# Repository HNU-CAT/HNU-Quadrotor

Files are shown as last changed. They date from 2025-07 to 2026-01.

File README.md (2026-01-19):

# HNU-Quadrotor

<figure>
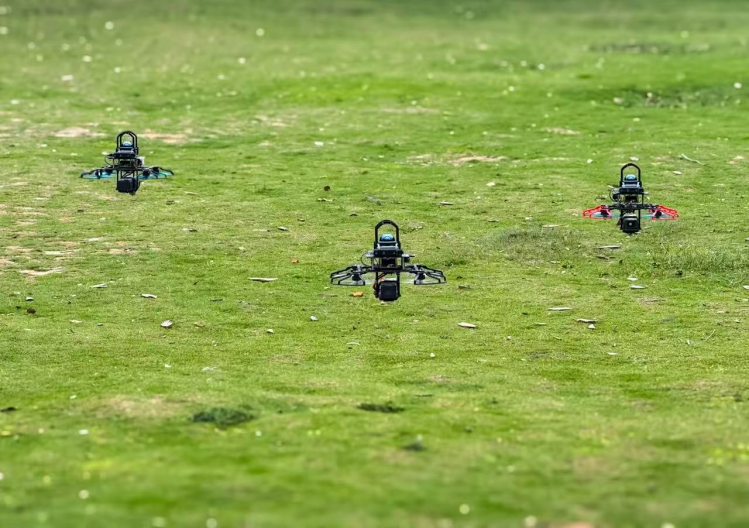
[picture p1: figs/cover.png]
    
    <figcaption>Three drones flying in the wild</figcaption>
</figure>

<figure>
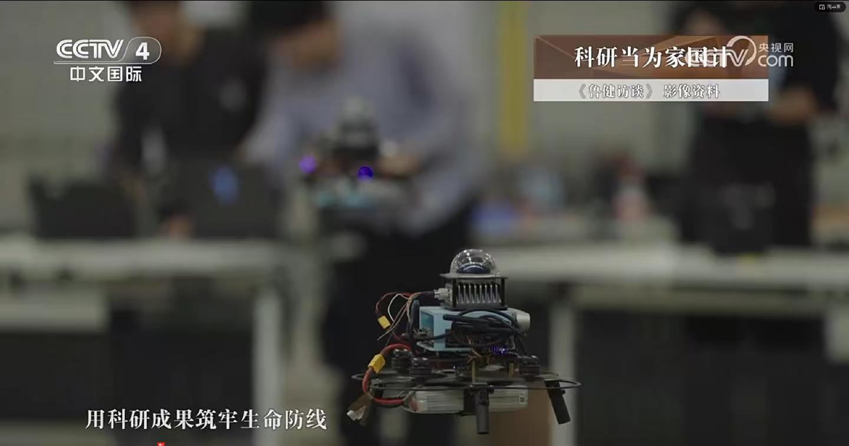
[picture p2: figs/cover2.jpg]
    
    <figcaption>Design of the first generation of drones</figcaption>
</figure>

<figure>
    
    <figcaption>>Four drones flying indoors</figcaption>
</figure>

**Author：**[WHDworld](https://github.com/WHDworld), [XXLiu-HNU](https://github.com/XXLiu-HNU)

## Provided Materials

We provide the following resources:

* Editable drafts and assemblies [./hardware](./hardware)

| Caption | Image Display |
|---|---|
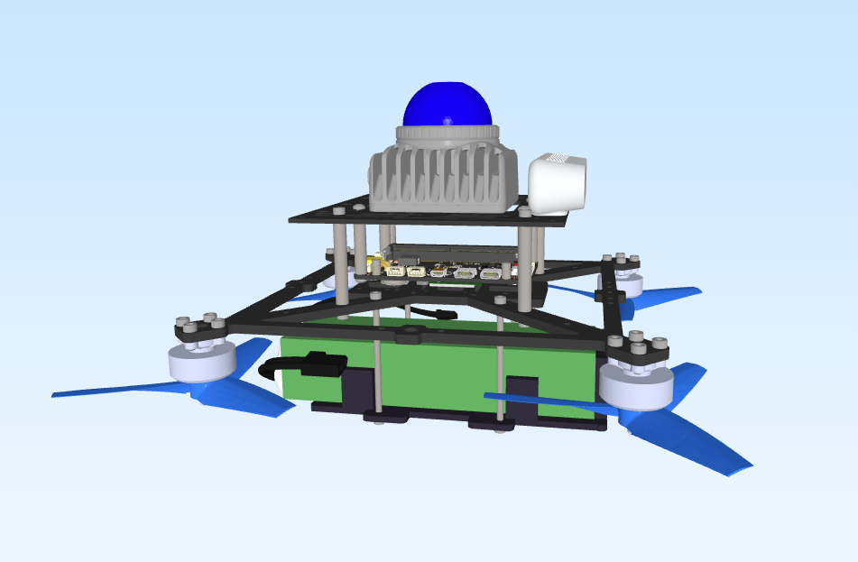
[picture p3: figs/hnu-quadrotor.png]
| UAV complete machine |  |
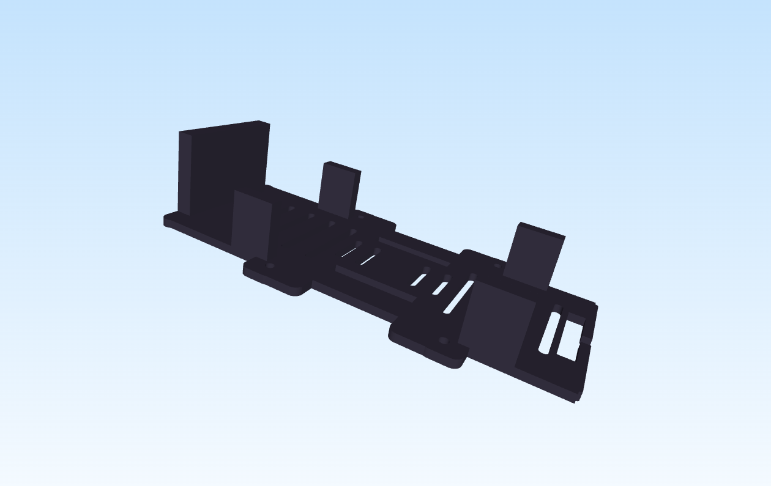
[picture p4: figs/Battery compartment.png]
| Battery compartment |  |
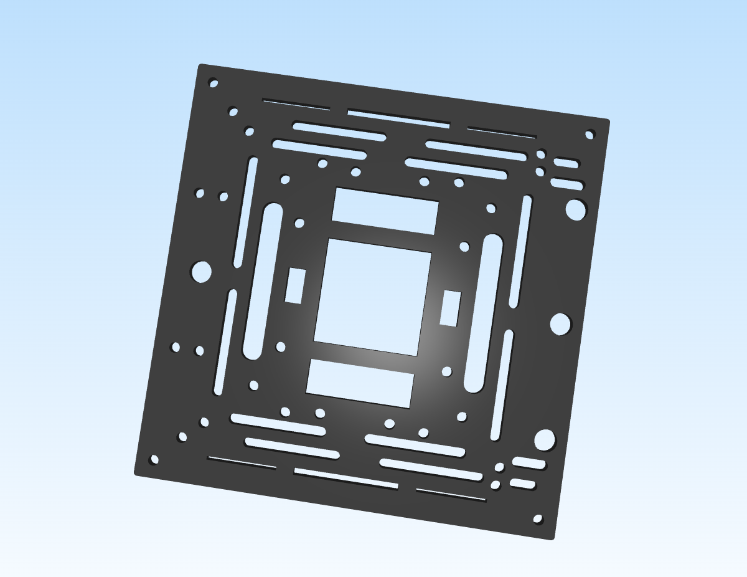
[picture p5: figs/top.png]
| Top view |  |
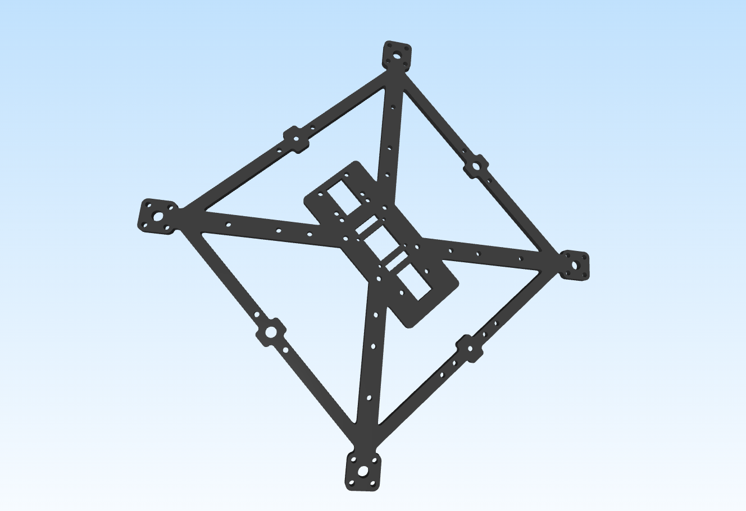
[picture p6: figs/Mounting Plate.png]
| Mounting plate |  |
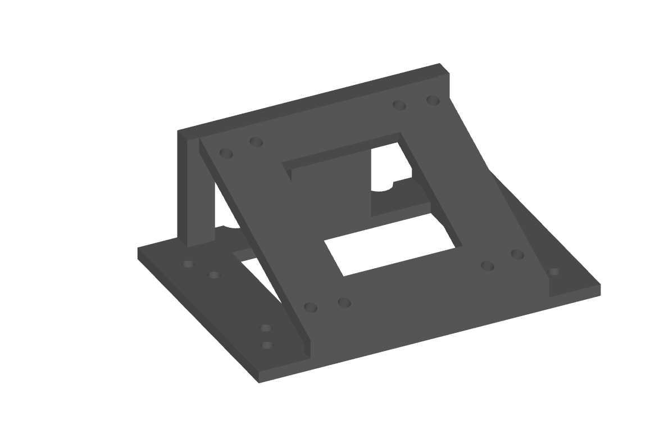
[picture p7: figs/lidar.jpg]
| LiDAR installation |  |

## Hardware Breakdown

The hardware structure is illustrated below:

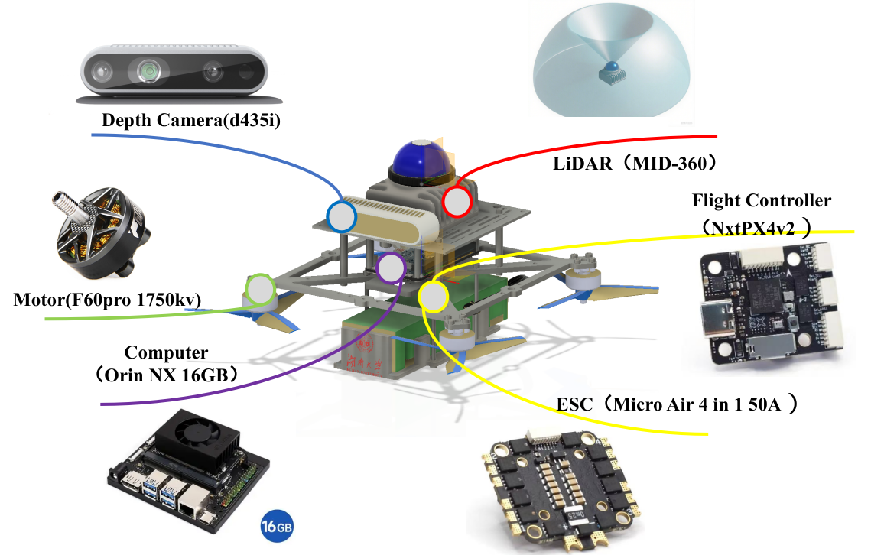
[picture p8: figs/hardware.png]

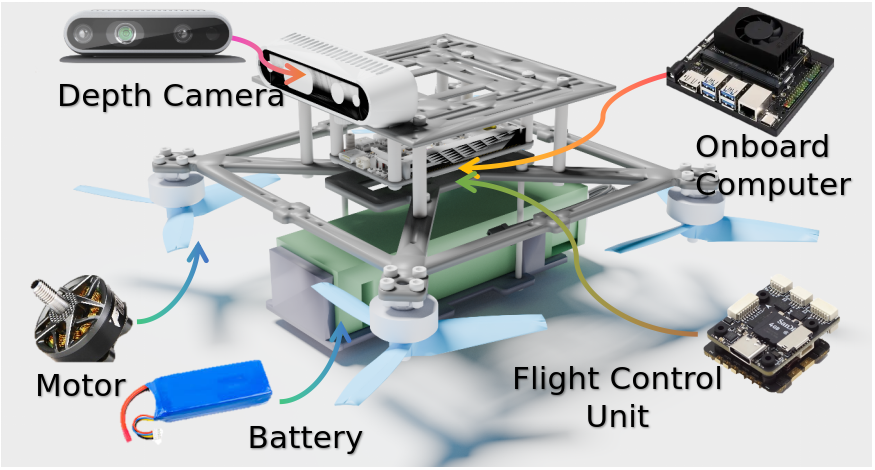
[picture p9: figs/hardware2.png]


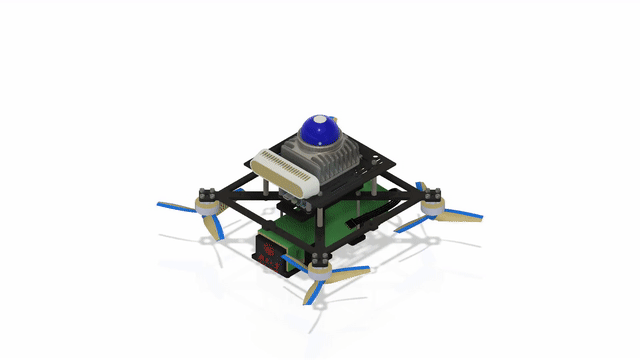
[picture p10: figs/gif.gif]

## Bill of Materials

| Name | Type |
| --- | --- |
| LiDAR | Livox MID360 |
| Depth Camera | Realsense D435i |
| Onboard Computer | Orin NX |
| Motor | T-Motor F60 Pro KV1750 |
| Propeller |  GEMFAN 5043 |
| ESC | Micro Air  4 in 1 50A |
| Battery | DualSky 3300mAh 6S XP-3300HED |
| Flight Controller | NxtPx4 v2 |
| RC | Radiolink AT9S |
| Receiver | Radiolink R12DSM |

## Use NUC as Onboard Computer
If you want to use the NUC as an onboard computer, you only need to install an additional top plate.

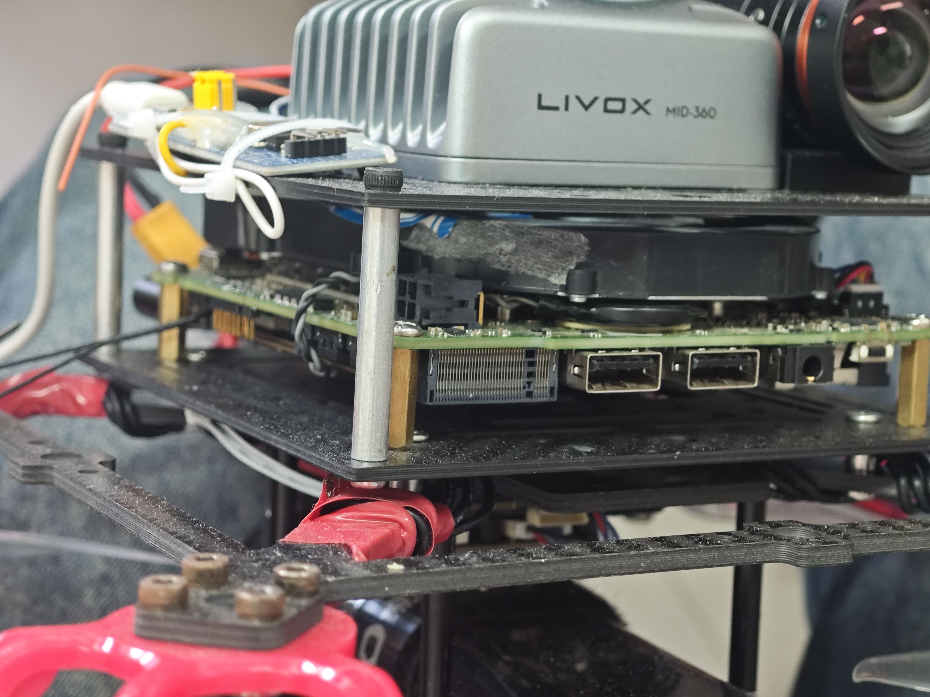
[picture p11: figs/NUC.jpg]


## Optional sensor

To enhance flight stability and safety, especially in complex environments, we support the integration of additional sensors.

Optical Flow Sensor
We highly recommend adding an Optical Flow Sensor (e.g.,MTF-01) to the bottom of the airframe.

Safety Backup: In scenarios where primary positioning (GPS or LiDAR-SLAM) is lost or degrades, the optical flow sensor provides high-frequency velocity feedback.

Fly-away Prevention: This ensures the drone can maintain a stable hover and prevents the aircraft from drifting or "flying away" due to state estimation failure.

Optional sensor layout

## Acknowledgments

When designing, we referred to the [super-hardware](https://github.com/hku-mars/SUPER-Hardware), [UniQuad](https://github.com/HKUST-Aerial-Robotics/UniQuad), [Fast-Drone-250](https://github.com/ZJU-FAST-Lab/Fast-Drone-250) projects and would like to express our sincere gratitude for this.

Gratitude to all contributors: Huidong Wang, Xingxun  Liu, Shaojie Li.

## Contact Us

If you have any questions about hardware or any other questions you want to consult, please contact us: liuxingxun@hnu.edu.cn

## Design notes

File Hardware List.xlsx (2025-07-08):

硬件 | 型号
机载电脑 | Nvidia ORIN NX
深度相机 | Realsense D435i
激光雷达 | Livox Mid 360
飞控 | NxtPX4v2
电调 | 微空四合一50A
电机 | TMOTOR F60 pro KV1750
电池 | 双天 6s 3300mah
遥控器 | 乐迪遥控器at9s PRO

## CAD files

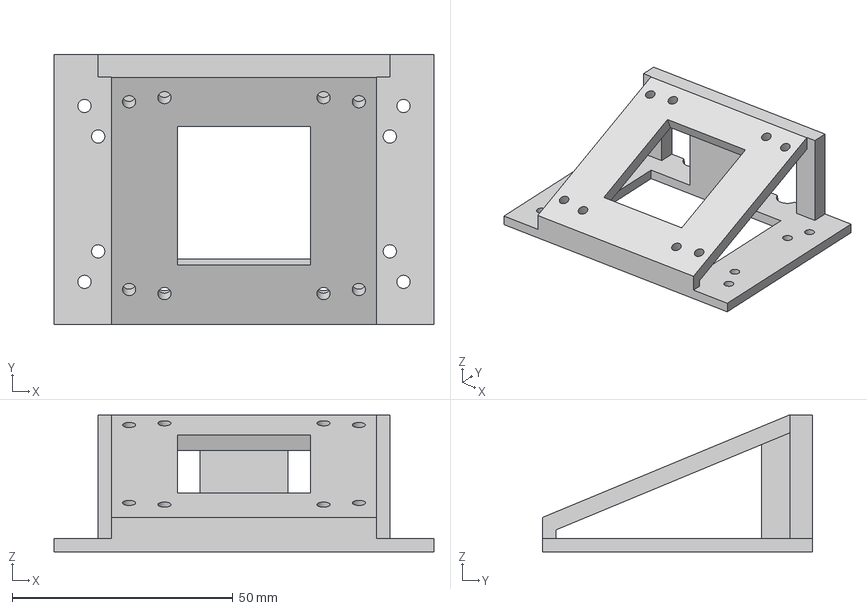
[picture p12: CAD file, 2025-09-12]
hardware/激光雷达安装板 v15.step
86.0 x 61.0 x 31.0 mm

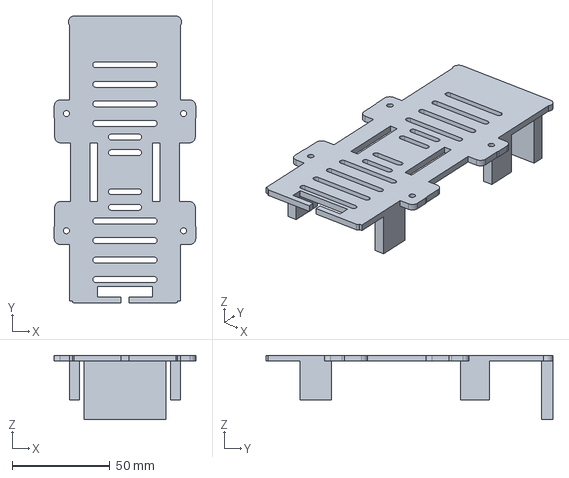
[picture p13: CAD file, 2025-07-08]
hardware/电池盒子.step
72.5 x 147.0 x 33.0 mm

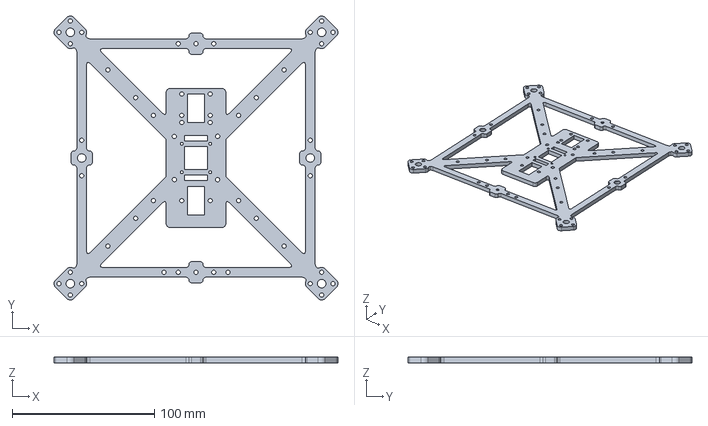
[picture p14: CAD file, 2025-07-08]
hardware/安装板.step
199.8 x 199.8 x 4.00 mm

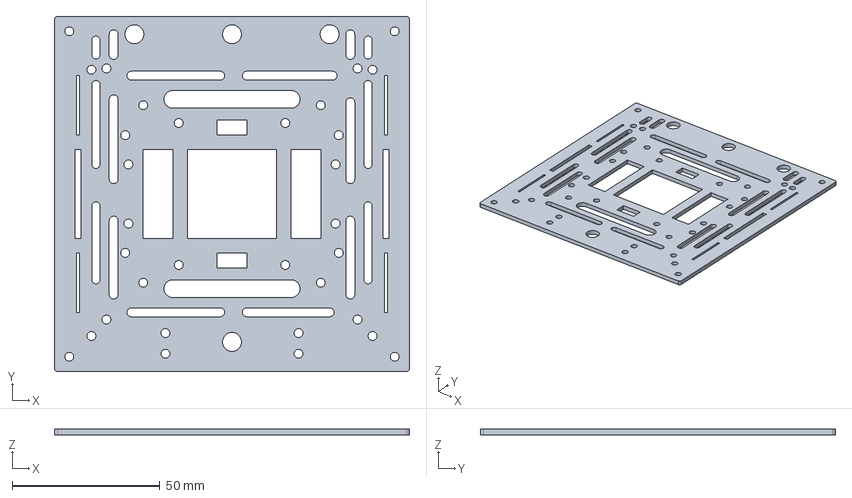
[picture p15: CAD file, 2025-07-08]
hardware/电脑雷达相机安装板.step
120.0 x 120.0 x 2.00 mm

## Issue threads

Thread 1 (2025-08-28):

安装相关资讯

jisuweng, 2025-08-28:
1.大佬请问有没有安装的铜柱的规格呢
2.请问有没有视频中斜装mid360的底座和360的保护罩的图纸呢
3.请问有没有桨保的图纸呢

谢谢大佬了

cn-ryw, 2025-09-01:
借个楼，谢谢！请问NX上Fast-drone-250和SUPER的配置能出一个教程吗？或者有什么可以供参考的？（NX的CPU算力低，而且ARM架构和GPU的调用有很多和NUC不同）

XXLiu-HNU, 2025-09-07:
1. 铝柱的规格如下：

2. 链接：

3.[购买链接](https://item.taobao.com/item.htm?id=574989413314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)

XXLiu-HNU, 2025-09-07:
> 借个楼，谢谢！请问NX上Fast-drone-250和SUPER的配置能出一个教程吗？或者有什么可以供参考的？（NX的CPU算力低，而且ARM架构和GPU的调用有很多和NUC不同）

你好，目前实验室NUC和NX均在使用，总体来说区别并不大。以EGO-Planner为例，需要把定位（VINS ）改为GPU版本，规划和控制跑在NX上并没有那么吃力，许多环境的问题网上已经有很多教程了，可以参考这个系列：[Jetson Orin NX 开发指南](https://blog.csdn.net/qq_44998513/article/details/133754589?spm=1001.2014.3001.5502)

jisuweng, 2025-09-09:
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

再问一下，请问我们使用的是orin nx的达妙载板，和底板的孔位能对上么

XXLiu-HNU, 2025-09-09:
> 再问一下，请问我们使用的是orin nx的达妙载板，和底板的孔位能对上么

可以的，我们就是用的达妙的

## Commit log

2025-09-12 upload lidar
    [激光雷达安装板 v15.step]
2026-01-19 Document optional sensor for enhanced flight stability
    Added section on optional sensor integration for flight stability.
